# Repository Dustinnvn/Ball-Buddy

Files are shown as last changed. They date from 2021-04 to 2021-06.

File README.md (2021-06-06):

<p align="center">
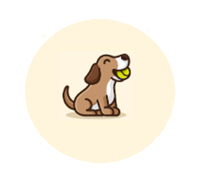
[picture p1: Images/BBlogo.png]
  
</p>

<h1 align="center">Ball Buddy :softball: </h1>

<!-- TABLE OF CONTENTS -->
<details open="open">
  <summary>Table of Contents</summary>
  <ol>
    <li><a href="#about-the-project">About The Project</a></li>
    <li><a href="#key-features">Key Features</a></li>
    <li><a href="#documentation">Documentation</a>
        <ul>
        <li><a href="#cad">CAD</a></li>
        <li><a href="#code">Code</a></li>
      </ul>
    </li>
    <li><a href="#materials">Materials</a></li>
    <li><a href="#progress">Progress</a></li>
    <li><a href="#contact">Contact</a></li>
  </ol>
</details>

<!-- ABOUT THE PROJECT -->
## About The Project

Ball Buddy is a pet ball launcher developed in my senior design class. It is inspired by a teammates dog which has separation anxiety, which would become exacerbated after work from home is lifed. In response we created a smart ball launcher so that we could help pets keep in touch with their owners from far away.

My main repsonibilites are in charge of designing and coding the ball recovery system. For the chassis design I will be working together with one of my teammates, Jason. I will also be helping on the webapp devlopment by creating a functional backend and database to control the ball recovery system.

## Key Features 
* Autonomous ball recovery and launch
* Controllable through an app or webpage
* 180 degree rotational and launch angles
* Saftey sensors to avoid injury
* Camera to view pets and launch trajectory 

## Documentation 
The CAD designs and code are a work in progress and will have continual updates. Currently the designs are focused for the ball recovery system but will eventually include the entire Ball Buddy. The code is for both the ball recovery system and ball launcher. Additional Raspberry pi code is also featured for software debugging.

### CAD 
All current CAD designs are in the Ball System V1 and V2. V1 was the first mockup design I created for the ball recovery system. It utilized a chain and gear mechanic to have simple stepper motor utilization. This design however was unable to adjust to any future changes to the ball buddy and was scrapped for the current V2 design. The V2 design is based on a CNC/3D printer using gantry rails, pulleys and stepper motors to control the x,y, and z axis. With this new design it is possible to move the ball in any  position within the frame and have room to adjust for other parts. Most parts were redesigned from V1 but I did keep the ball setter hand and ball que. 

All parts were designed in Solidworks and can be converted to STL for printing.

### Code 
The MasterStepper is the current code used to control all 5 stepper motors in the ball recovery system. This includes motor to spin the ball que, 2 motors to lift up the X-axis, and 2 motors to control the X-axis ball setter hand. The code has funcitons to adjust distance and individual controls for each axis. It also takes serial input to move and  outputs serial data for debugging. This code is ran on a Arduino Uno R3.

Utilizing the Arduino for the brute work, I used the Raspberry Pi for the main processing of data. While our software developer worked on setting up a permanent server, I began to develop groundwork Pi code to work with our Arduino. Since I utilized serial communication for the Arduino, I used a usb connection to the Raspberry Pi for both microcontrollers to talk to each other. With communication between the two microcontrollers established, I used the html library in python to create a basic webpage that could send commands to the Pi. This let me access the Pi from a webpage that would send serial data to the arduino which could then relay data back for the Pi to process. The Pi python code was ran on a Raspberry Pi 4

## Materials 

Part| Price | System
------------ | -------------| -------------
Pixy2 Camera | $60 | Ball Launcher
Camera Module   | $50 | Ball Launcher
Raspberry Pi| $40 | App
Arduino Mega 2560 | $15 | Ball Recovery & Ball Launcher
Nema 17 Stepper Motor (x3)| $17 (x3) | Ball Recovery
Nema 17 with T8 Screw Lead (x2)| $15 (x2) | Ball Recovery
BIQU A4988 Motor Drivers| $10 | Ball Recovery
4 400mm 2020 V type Gantry Rai| $34 | Ball Recovery
2 700mm 2040 V type Gantry Rail | $31 | Ball Recovery
2 350mm 2040 V Type Gantry Rail | $20 | Ball Recovery
6mm Eccentric Spacers | $10 | Ball Recovery
Assorted M2-6 Screws and Nuts | $30 | Ball Recovery
5m by 6mm Timing Belt Kit | $16 | Ball Recovery
BTS7960 Motor Driver | $13 | Ball Launcher
Electromagnetic Solenoid (x2) | $16 (x2) | Ball Launcher
**Total Amount Spent**| $442 | |

## Progress 

<p align="left">
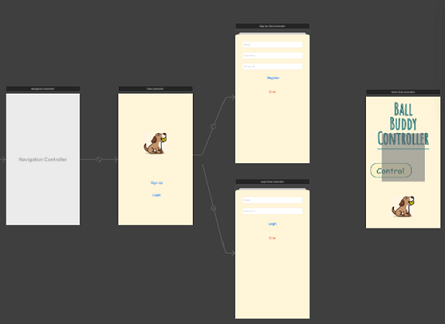
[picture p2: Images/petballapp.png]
  
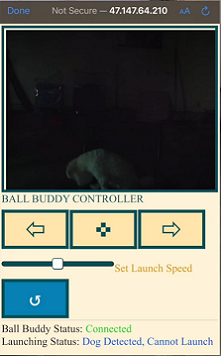
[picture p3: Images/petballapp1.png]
  
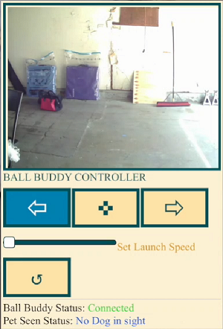
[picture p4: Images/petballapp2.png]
  
</p>

The first image is the log in screen and the following pannels that follow to log in and register. After registering or logging in, the user is then proceeded to the controls page which features a camera to show what the ball launcher is looking at. There are buttons at bellow the screen to move the launcher left and right. There is also a slider below to choose the amount of speed and distance the ball will be launched. The final button at the bottom is used to reload the ball and set up for the next launch. 

At the bottom there are also 2 status displays to give the user updates on the ball launcher. The first status confirms that the ball launcher is online and connceted to the application. The second status is to confirm which cylce the ball launcher is at. Currently the ball launcher is in the launch phase and since the sensor detects a dog, it will not launch until the dog moves away from the launcher. 

<p align="left">
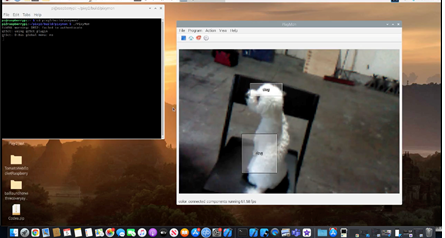
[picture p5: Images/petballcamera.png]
  
</p>

The sensors we used to detect humans and dogs is the nexy2 pixy camera. It has its own software similar to openCV that takes samples and then categorizes them accordingly to the user preference. In this case, we took Jenny the dog as our sample and gave her the identifier "dog". Using multiple samples we are able to have the camera recognize Jenny as a dog and are then futher able to work upon this data to create our saftey sensor.

<!-- CONTACT -->
## Contact 

Dustin Nguyen - dustinnvn@gmail.com

Project Link: [https://github.com/Dustinnvn/Ball-Buddy](https://github.com/Dustinnvn/Ball-Buddy)

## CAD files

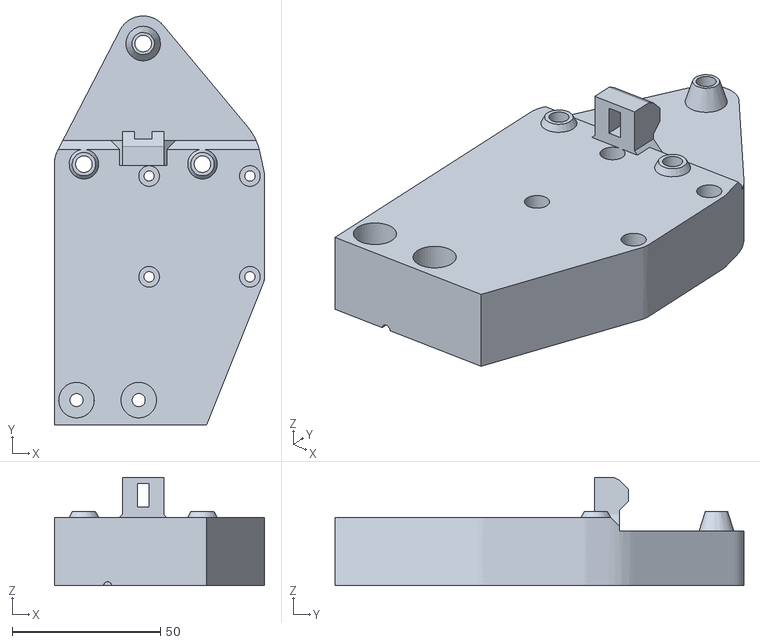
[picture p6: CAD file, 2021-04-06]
Ball System V2/CARRIAGE pieces/CARRIAGEfront.stl
71.0 x 138.0 x 36.5

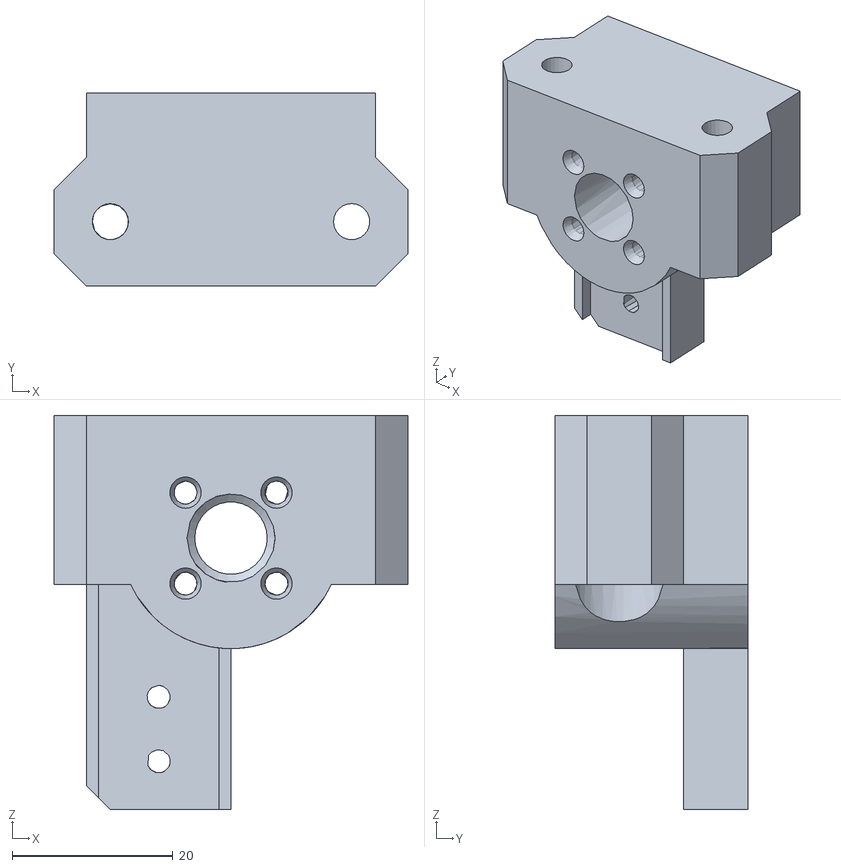
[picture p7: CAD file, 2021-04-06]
Ball System V2/X-Z ASSEMBLY pieces/RodHolder1.stl
44.0 x 24.0 x 49.0

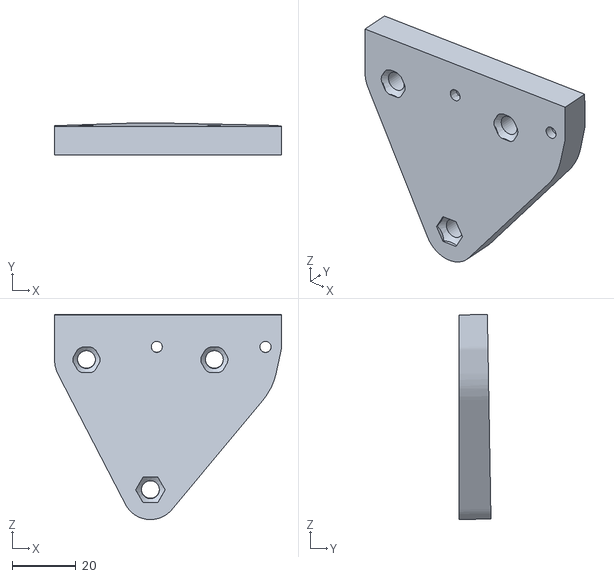
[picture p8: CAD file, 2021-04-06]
Ball System V2/CARRIAGE pieces/CARRIAGEback.stl
71.0 x 10.00 x 64.2

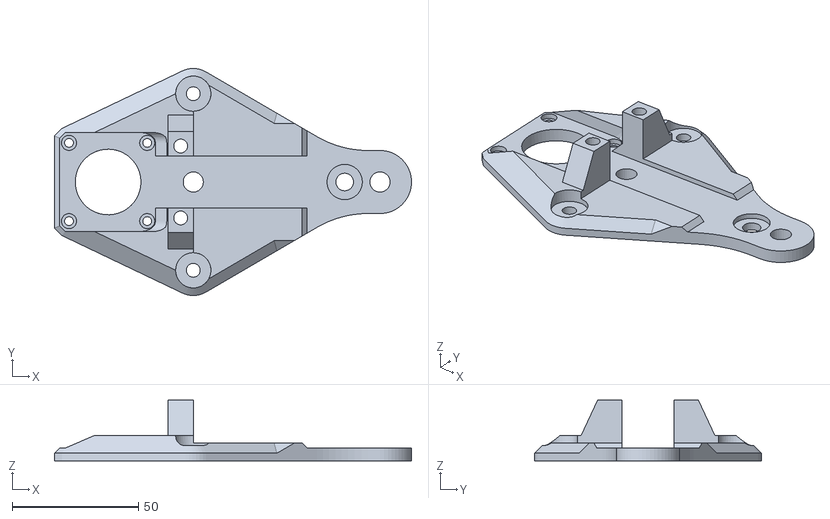
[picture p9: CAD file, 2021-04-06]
Ball System V2/X-Z ASSEMBLY pieces/Xfrontplate2.stl
141.5 x 90.0 x 24.0

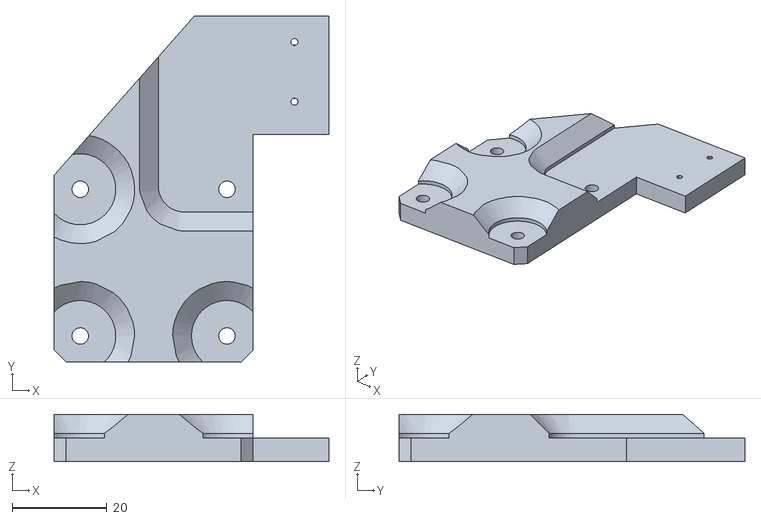
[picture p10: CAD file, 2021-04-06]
Ball System V2/X-Z ASSEMBLY pieces/XMotorMount2.stl
58.0 x 73.1 x 10.0

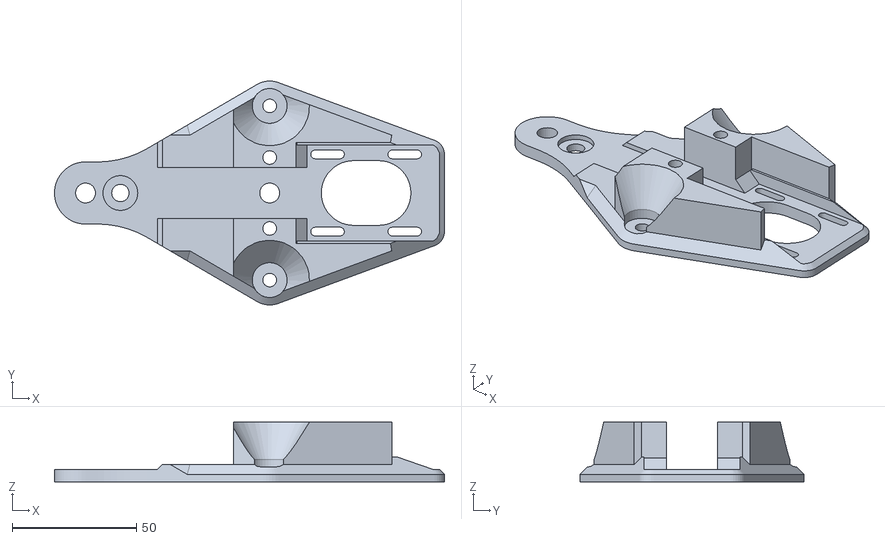
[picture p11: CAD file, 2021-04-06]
Ball System V2/X-Z ASSEMBLY pieces/Xfrontplate1.stl
156.7 x 90.0 x 24.0

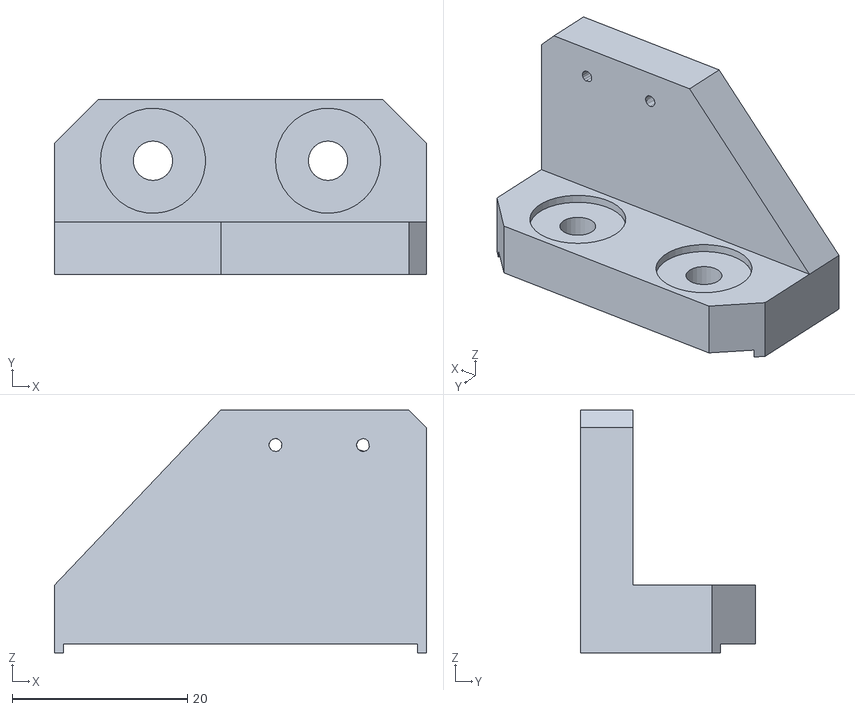
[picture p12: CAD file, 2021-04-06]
Ball System V2/X-Z ASSEMBLY pieces/XLbracket2.stl
42.5 x 20.0 x 27.8

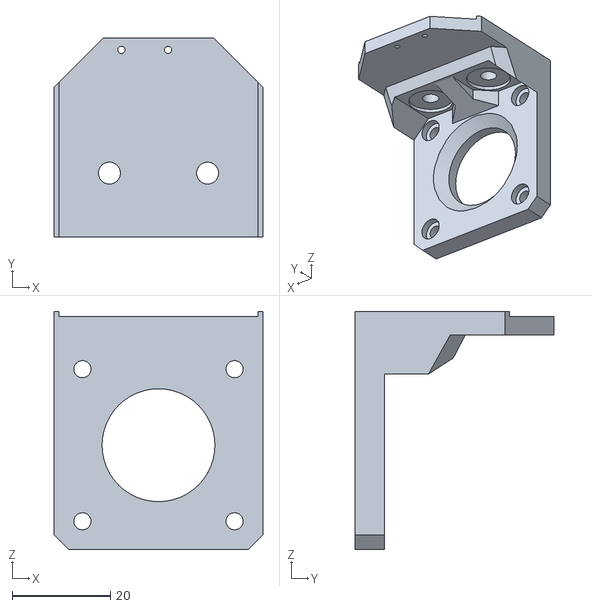
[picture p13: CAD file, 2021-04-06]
Ball System V2/X-Z ASSEMBLY pieces/XMotormount.stl
42.5 x 40.5 x 48.5

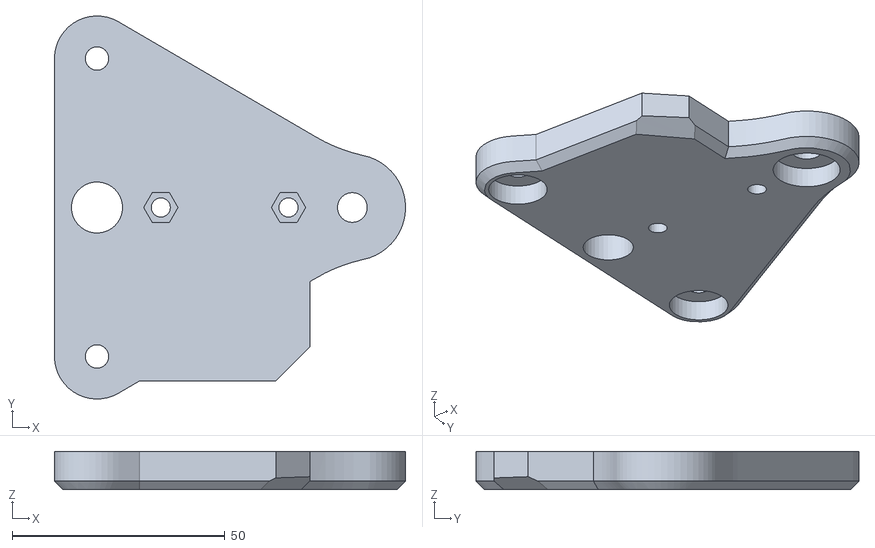
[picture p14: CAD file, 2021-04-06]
Ball System V2/X-Z ASSEMBLY pieces/Xbackplate2.stl
82.5 x 90.0 x 9.00

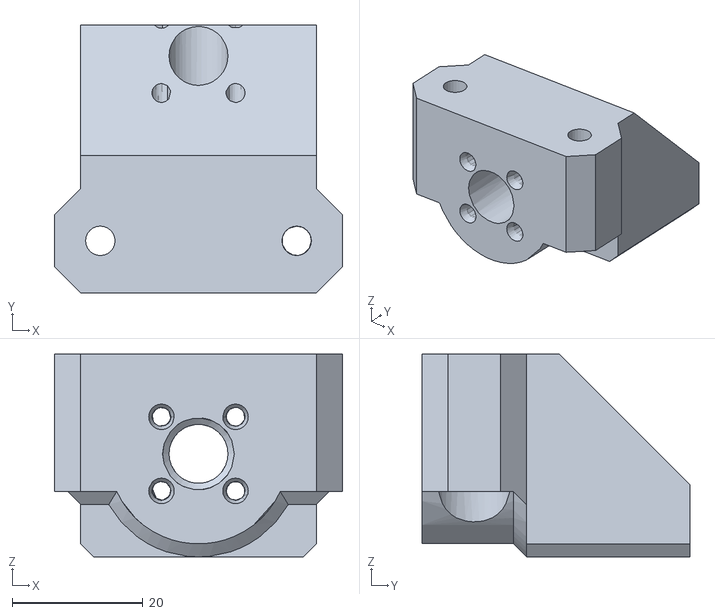
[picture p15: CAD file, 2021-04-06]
Ball System V2/X-Z ASSEMBLY pieces/RodHolder2.stl
44.0 x 41.0 x 31.0

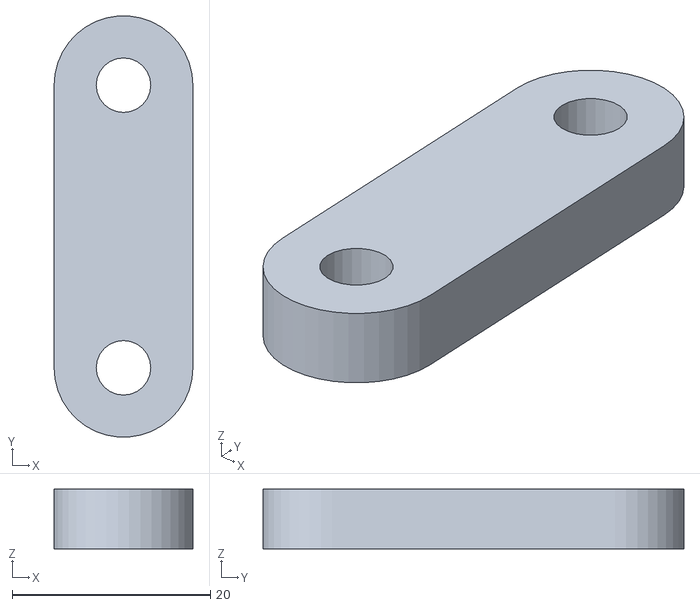
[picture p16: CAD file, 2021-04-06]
Ball System V2/X-Z ASSEMBLY pieces/Xfrontplate1Clip.stl
14.0 x 42.5 x 6.00

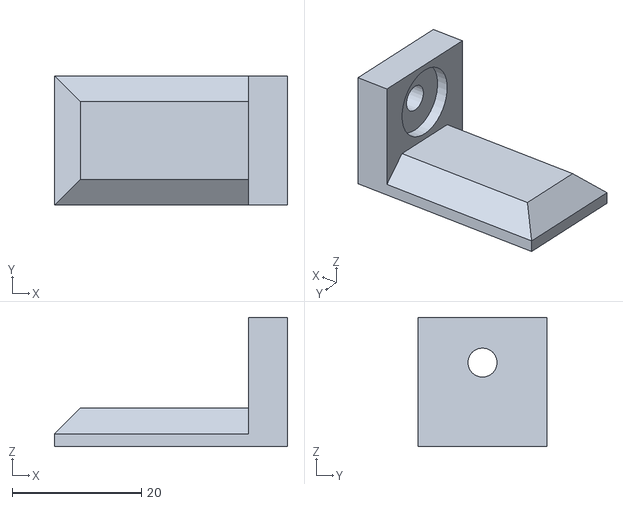
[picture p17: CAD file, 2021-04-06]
Ball System V2/X-Z ASSEMBLY pieces/Xspacescrew.stl
36.0 x 20.0 x 20.0

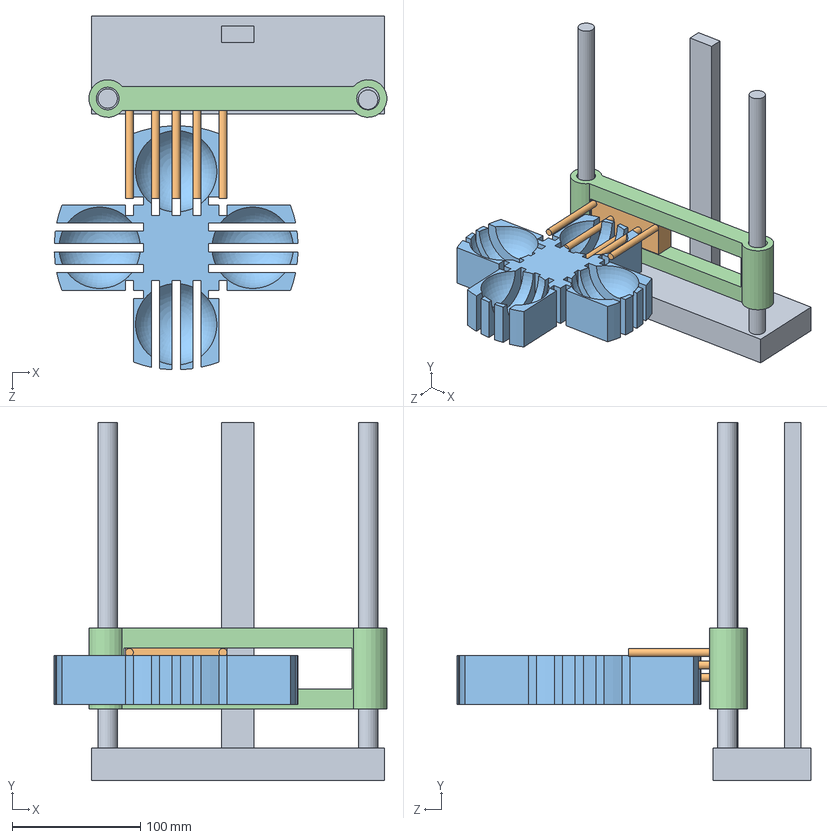
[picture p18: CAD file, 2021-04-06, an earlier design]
Ball System V1/PetBallAssemblyV2.SLDASM
259.6 x 279.4 x 275.9 mm
BallSetterStandV1
BallSetterHandV1
BallQueTrayV2
BallSetterZBraceV2

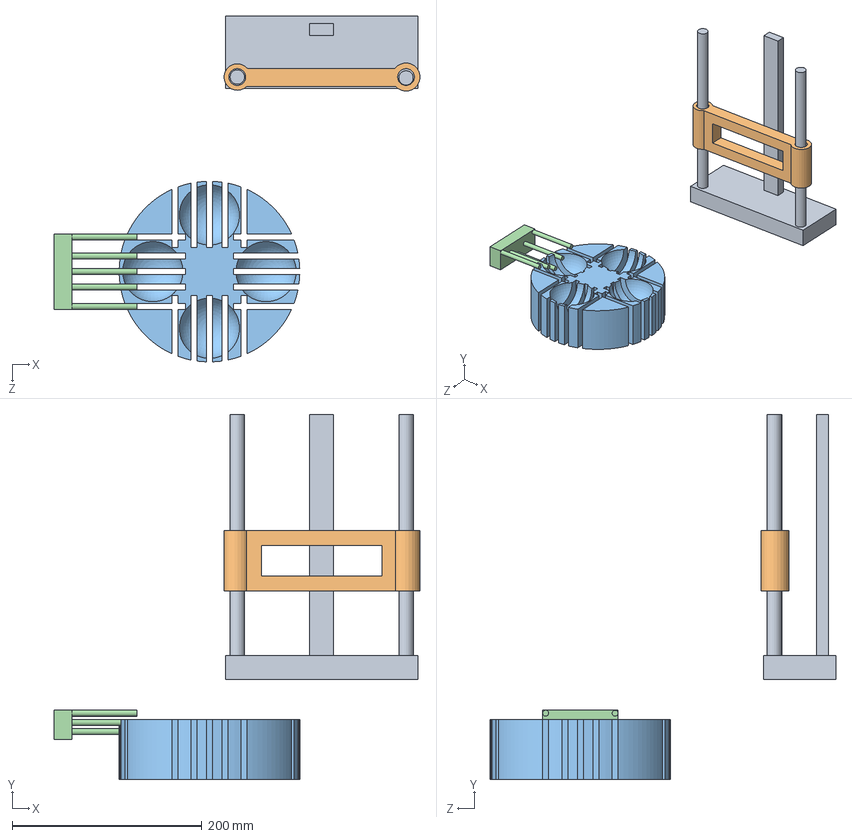
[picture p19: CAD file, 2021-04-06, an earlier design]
Ball System V1/PetBallAssemblyV1.SLDASM
385.7 x 385.2 x 364.5 mm
BallSetterStandV1
BallSetterZBraceV1
BallQueTrayV1
BallSetterHandV1

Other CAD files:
Ball System V2/X-Z ASSEMBLY pieces/Xbackplate1.stl
Ball System V1/BallQueTray/BallQueTrayV3.SLDPRT
Ball System V1/BallSetterBrace/BallSetterZBraceV1.SLDPRT
Ball System V1/BallQueTray/BallQueTray.SLDPRT
Ball System V1/BallQueTray/BallQueTrayTest.SLDPRT
Ball System V1/BallQueTray/BallQueTrayV1.SLDPRT
Ball System V1/BallQueTray/BallQueTrayV1.STL
Ball System V1/BallQueTray/BallQueTrayV2.SLDPRT
Ball System V1/BallQueTray/BallQueTrayV2.STL
Ball System V1/BallSetterBrace/BallSetterStandV1.SLDPRT
Ball System V1/BallSetterBrace/BallSetterZBraceV2.SLDPRT
Ball System V1/BallSetterBrace/BallSetterZBraceV2.STL
Ball System V1/BallSetterBrace/BallSetterZBraceV3.SLDPRT
Ball System V1/BallSetterBrace/BallSetterZBraceV3.STL
Ball System V1/BallSetterHand/BallSetterHandV1.SLDPRT
Ball System V1/BallSetterHand/BallSetterHandV1.STL
Ball System V1/BallSetterHand/BallSetterHandV2.SLDPRT
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

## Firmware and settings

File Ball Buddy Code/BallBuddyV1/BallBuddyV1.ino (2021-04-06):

const int stepPinT = 7; 
const int dirPinT = 8; 
const int stepPinX = 5; 
const int dirPinX = 6; 
const int stepPin = 3; 
const int dirPin = 4; 
 
 
int R_EN1 = 13; //Motor 1
int R_PWM1 = 9;
int L_EN1 = 12;
int L_PWM1 = 10;
 
//int R_EN2 = 12; //Motor 2
//nt R_PWM2 = 10;
//int L_EN2 = 13;
//int L_PWM2 = 9;
 
int RELAY = 11; //Relay for Solenoid
 
long inputValue = 0; // store read value
 
      int Changed = 0; //for decieding direction of Y axis
      int Changed1 = 0; //for decieding direction of X axis
      int Changed2 = 0; //for decieding direction of XY Cycle 
unsigned long start, finished, elapsed;
      String input;
/////////////////////////////////////////////////
 
 
void setup() {
  // Sets the two pins as Outputs
  Serial.begin(9600); //open the serial port at 9600 bps
  pinMode(stepPinT,OUTPUT); 
  pinMode(dirPinT,OUTPUT);
  pinMode(stepPinX,OUTPUT); 
  pinMode(dirPinX,OUTPUT);
  pinMode(stepPin,OUTPUT); 
  pinMode(dirPin,OUTPUT);
 
 
 pinMode(R_EN1, OUTPUT);
 pinMode(R_PWM1, OUTPUT);
 pinMode(L_EN1, OUTPUT);
 pinMode(L_PWM1, OUTPUT);
 digitalWrite(R_EN1, HIGH);
 digitalWrite(L_EN1, HIGH);
 
 //pinMode(R_EN2, OUTPUT);
 //pinMode(R_PWM2, OUTPUT);
 //pinMode(L_EN2, OUTPUT);
 //pinMode(L_PWM2, OUTPUT);
 //digitalWrite(R_EN2, HIGH);
 //digitalWrite(L_EN2, HIGH);
 
 pinMode(RELAY, OUTPUT);
}
 
void motors50PWM_ON() {
  int i;
  start=millis();
 
  for (i = 0; i <= 120; i++) {
 
    analogWrite(R_PWM1, i);
    analogWrite(L_PWM1, 0);
 
    //analogWrite(R_PWM2, i);
    //analogWrite(L_PWM2, 0);
 
    delay(100);
  }
 
  analogWrite(R_PWM1, 100);
  analogWrite(L_PWM1, 0);
//  
//  analogWrite(R_PWM2, 100);
//  analogWrite(L_PWM2, 0);
 
  //delay(5000);
    Serial.println("Done 1/2");
 
}
 
void motors50PWM_OFF() {
 
  analogWrite(R_PWM1, 100);
  analogWrite(L_PWM1, 0);
//  
//  analogWrite(R_PWM2, 100);
//  analogWrite(L_PWM2, 0);
 
  //delay(5000);
 
  analogWrite(R_PWM1, 0);
  analogWrite(L_PWM1, 0);
 
  //analogWrite(R_PWM2, 0);
  //analogWrite(L_PWM2, 0);
  finished=millis();
  elapsed=finished-start-1000; //last number needs to change with delay(#)
  //Serial.println("Finished");
  Serial.println(elapsed);
  Serial.println("Done 2/2");
 
 
}
 
void Yaxis() {
  Serial.println("Start Y..");
 
  start=millis();
  if (Changed == 0) {
    digitalWrite(dirPin,HIGH);  //Enables the motor to move in a particular direction
  }
  if (Changed == 1) {
    digitalWrite(dirPin,LOW);
  }
  // Makes 200 pulses for making one full cycle rotation
  for(int x = 0; x < 5600; x++) { //5600 is one cylce up/down
 
    if ((x == 5599) && (Changed == 0)) {
        //digitalWrite(ledB,HIGH); //when we reach the desired distance we change directing and give off signal
        Changed = 1; 
        delay(1000);
      }
    else if ((x == 5599) && (Changed == 1)) {
        //digitalWrite(ledR,HIGH);
        Changed = 0;
        delay(1000);
      }    
 
 
    digitalWrite(stepPin,HIGH); 
    delayMicroseconds(1500); 
    digitalWrite(stepPin,LOW); 
    delayMicroseconds(1500);
  }
  finished=millis();
  elapsed=finished-start-1000; //last number needs to change with delay(#)
  //Serial.println("Finished");
  Serial.println(elapsed);
  //Serial.println();
 
}
///////////////////////////////////////////////////////////////////////////////////////////////////////
void Xaxis() {
  Serial.println("Start X..");
 
  start=millis();
  if (Changed1 == 0) {
    digitalWrite(dirPinX,HIGH);  //Enables the motor to move in a particular direction
  }
  if (Changed1 == 1) {
    digitalWrite(dirPinX,LOW);
  }
  // Makes 200 pulses for making one full cycle rotation
  for(int x = 0; x < 710; x++) { //5600 is one cylce up/down
 
    if ((x == 679) && (Changed == 0)) {
        //digitalWrite(ledB,HIGH); //when we reach the desired distance we change directing and give off signal
        Changed1 = 1; 
      }
    else if ((x == 679) && (Changed == 1)) {
        //digitalWrite(ledR,HIGH);
        Changed1 = 0;
 
      }
 
 
    digitalWrite(stepPinX,HIGH); 
    delayMicroseconds(1500); 
    digitalWrite(stepPinX,LOW); 
    delayMicroseconds(1500);
  }
  finished=millis();
  elapsed=finished-start-1000; //last number needs to change with delay(#)
  //Serial.println("Finished");
  Serial.println(elapsed);
  //Serial.println();
  delay(1000);
}
 
///////////////////////////////////////////////////////////////////////////////////////////////////////
 
void XYaxis() {
 
 
  Serial.println("Start XY..");
 
  if (Changed2 == 0) {                            //////PART 1 LOADING POSITION
    //if in the down left position
    Upcycle();  // GO  UP
    Serial.println("Finished Y... (1/1)");
    Serial.println("Ball Ready to be launched");
    Changed2 = 1;         // Move to the next phase (launch)
  }
  else if (Changed2 == 1) {
 
    Launch();
 
    Changed2 = 2;
  }
  else  {                                       //////PART 2 RECOVER POSITION
    //if in the top left position and launched ball
    Rightcycle();
    Serial.println("Finished X... (1/4)");    
 
    Downcycle();   // GO right - down-left
    Serial.println("Finished Y... (2/4)");
 
    Leftcycle();
    Serial.println("Finished X... (3/4)");
 
    Spins();
    Serial.println("Finished Spin... (4/4)");
 
    Serial.println("Ball Ready to be loaded");
 
    Changed2 = 0;
  }
 
}
///////////////////////////////////////////////////////////////////////////////////////////////////////////////
 
void Launch() {
 
 
  Serial.println("Start Launch...");
  motors50PWM_ON();
 
  Serial.println("Start Solenoid");
  digitalWrite(RELAY, HIGH);
  delay(500);
  digitalWrite(RELAY, LOW);
  delay(1500);
  motors50PWM_OFF();
}
void Cycle2() {
 
 
  Serial.println("Start XY..");
 
  Upcycle();  // GO  UP
  Serial.println("Finished Y... (1/1)");
  Serial.println("Ball Ready to be launched");
  delay(1000);       // Move to the next phase (launch)
  
  Launch();
 
  delay(1000);
  
  Rightcycle();
  Serial.println("Finished X... (1/4)");    
 
  Downcycle();   // GO right - down-left
  Serial.println("Finished Y... (2/4)");
 
  Leftcycle();
  Serial.println("Finished X... (3/4)");
 
  Spins();
  Serial.println("Finished Spin... (4/4)");
 
  Serial.println("Ball Ready to be loaded");
 
}
 
void Spins() {
  Serial.println("Start..");
  // Makes 200 pulses for making one full cycle rotation
  for(int x = 0; x < 51; x++) { //5600 is one cylce up/down
 
    if (x == 49) {
        //digitalWrite(ledB,HIGH); //when we reach the desired distance we change directing and give off signal
      }
 
 
    digitalWrite(stepPinT,HIGH); 
    delayMicroseconds(3500); 
    digitalWrite(stepPinT,LOW); 
    delayMicroseconds(3500);
  }
  //Serial.println("Finished");
  //Serial.println();
  delay(1000);
 
}
 
void loop() {
 
  if (Serial.available()){
    input = Serial.readStringUntil('\n');         //////////////////////////////////// START POSITION= BOTTOM LEFT ____ LAUNCH POSITION= TOP RIGHT
 
    if (input.equals("g")) {
      Serial.println("start motors");
      //motors50_ONPWM();
    }
    else if (input.equals("d")){           ////   DOWN   = d
      Serial.println("Going down");
      Downcycle();
    }
    else if (input.equals("u")){
      Serial.println("Going up");        ////   UP     = u
      Upcycle();
    }
    else if (input.equals("1")){      ////   RIGHT  = 1
      Serial.println("Going right");
      Rightcycle();
    }
    else if (input.equals("2")){     ////    LEFT   = 2
      Serial.println("Going left");
      Leftcycle();
    }
    else if (input.equals("3")){     ////    TRAY SPIN   = 3
      Serial.println("Spin");
      Spins();
    }
    else if (input.equals("4")){
      Serial.println("XY Cycle");      ////  UP-RIGHT/ DOWN-LEFT    = 4
       XYaxis();
    }
    else if (input.equals("l")){           ////   Launching Sequence   = L
      Serial.println("Launch Cycle");
      Launch();
    }
    
    else if (input.equals("s")){           ////   Launching Sequence   = L
      Serial.println("Launch Cycle");
      Cycle2();
    }
    Serial.println("Finished");
 
  }
 
}
 
///////////////////////////////////////////////////////////////////////////////////////////////////////////////
 
 
void XYcycle() {
  XYaxis();
 
  //Serial.println("XY Cylcle  Finished");
}
void Downcycle() {
  Changed = 1;
  Yaxis();
  Changed = 0;
  //Serial.println(" Down Cylcle Finished");
}
void Upcycle() {
  Changed = 0;
  Yaxis();
  Changed = 0;
  //Serial.println(" Up Cylcle Finished");
}
void Rightcycle() {
  Changed1 = 1;
  Xaxis();
  Changed1 = 0;
  //Serial.println(" Right Cylcle Finished");
}
void Leftcycle() {
  Changed1 = 0;
  Xaxis();
  Changed1 = 0;
  //Serial.println(" Left Cylcle Finished");
}

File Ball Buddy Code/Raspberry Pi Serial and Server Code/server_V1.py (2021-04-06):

#!/usr/bin/env python3
import serial
import time
#import RPi.GPIO as GPIO
import os
from http.server import BaseHTTPRequestHandler, HTTPServer

host_name = '192.168.86.33'  # IP Address of Raspberry Pi
host_port = 8000


def getTemperature():
    temp = os.popen("/opt/vc/bin/vcgencmd measure_temp").read()
    return temp


class MyServer(BaseHTTPRequestHandler):

    def do_HEAD(self):
        self.send_response(200)
        self.send_header('Content-type', 'text/html')
        self.end_headers()

    def _redirect(self, path):
        self.send_response(303)
        self.send_header('Content-type', 'text/html')
        self.send_header('Location', path)
        self.end_headers()

    def do_GET(self):
        html = '''
           <html>
           <head>  
           <head>  
           <body
            style="width:960px; margin: 20px auto;">
           <h1>Welcome to my Pet Ball</h1>
           <p>Current CPU temperature is {}</p>
           <p>Click on a button to move the ball launcher</p>  
           <form action="/" method="POST">
               Move X Motor:
               <input type="submit" name="submit" value="Right">
               <input type="submit" name="submit" value="Left">
           </form>
           <form action="/" method="POST">
               Move Y Motor:
               <input type="submit" name="submit" value="Up">
               <input type="submit" name="submit" value="Down">
               <input type="submit" name="submit" value="Cycle">

           </form>
           <button onclick="getElementById('demo').innerHTML = Date()">What is the time?</button>
           <p id="demo"></p>
           </body>
           </html>
        '''
        temp = getTemperature()
        self.do_HEAD()
        self.wfile.write(html.format(temp[5:]).encode("utf-8"))

    def do_POST(self):

        content_length = int(self.headers['Content-Length'])
        post_data = self.rfile.read(content_length).decode("utf-8")
        post_data = post_data.split("=")[1]
        #the input is coded as the button names aka post data d-down, u-up, 1-right, 2-left, 3-spin
        if post_data == 'Up':
            ser.write('u'.encode())
            time.sleep(1)
           
        elif post_data == 'Down':
            ser.write('d'.encode())
            time.sleep(1)
        elif post_data == 'Right':
            ser.write('1'.encode())
            time.sleep(1)
        elif post_data == 'Left':
            ser.write('2'.encode())
            time.sleep(1)
        elif post_data == 'Cycle':
            ser.write('4'.encode())
            time.sleep(1) 

        print("MODE is {}".format(post_data))
        self._redirect('/')  # Redirect back to the root url


# # # # # Main # # # # #

if __name__ == '__main__':
    
    ser = serial.Serial("/dev/ttyACM0", 9600, timeout=1) #change ACM number as found from ls /dev/tty/ACM*
    ser.flush()
    http_server = HTTPServer((host_name, host_port), MyServer)
    print("Server Starts - %s:%s" % (host_name, host_port))
    
    try:
        http_server.serve_forever()
    except KeyboardInterrupt:
        http_server.server_close()

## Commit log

2021-04-06 Add files via upload
    Added CAD designs used for Ball Buddy
    [BallQueTray.SLDPRT, BallQueTrayTest.SLDPRT, BallQueTrayV1.SLDPRT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]
2021-04-06 Add files via upload
    Carriage CAD Design
    [CARRIAGEback.stl, CARRIAGEfront.stl]
2021-04-06 Add files via upload
    X-axis and Z-axis Motor Mounts
    [RodHolder1.stl, RodHolder2.stl, XLbracket2.stl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]
2021-04-06 Ball Que Tray CAD designs
    [BallQueTray.SLDPRT, BallQueTrayTest.SLDPRT, BallQueTrayV1.SLDPRT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]
2021-04-06 Ball Setter Brace CAD Designs
    [BallSetterStandV1.SLDPRT, BallSetterZBraceV1.SLDPRT, BallSetterZBraceV2.SLDPRT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]
2021-04-06 Ball Setter Hand CAD Design
    [BallSetterHandV1.SLDPRT, BallSetterHandV1.STL, BallSetterHandV2.SLDPRT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]
2021-04-06 Pet Ball CAD Design Assembled
    [PetBallAssemblyV1.SLDASM, PetBallAssemblyV2.SLDASM]
2021-04-06 Raspberry Pi Implementaion
2021-04-06 Raspberry Pi Implementation
